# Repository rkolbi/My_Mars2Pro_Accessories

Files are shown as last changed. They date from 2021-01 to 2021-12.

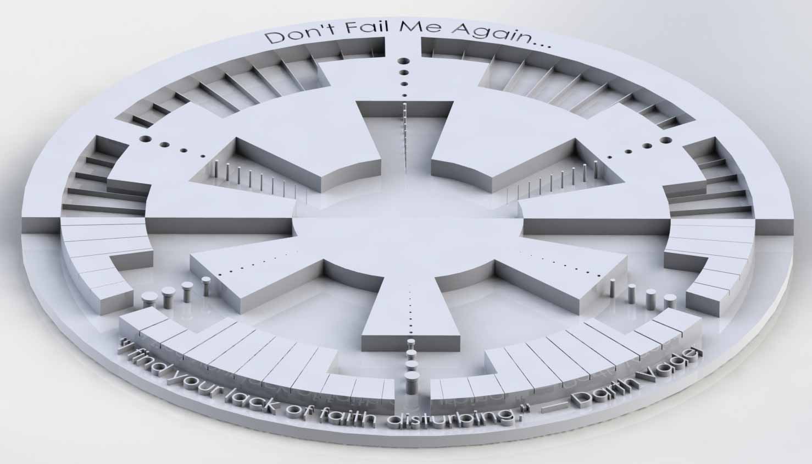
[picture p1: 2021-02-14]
Resin_exposure_testing/STLs/Imperial test/Imperial-resin-v4-c.jpg

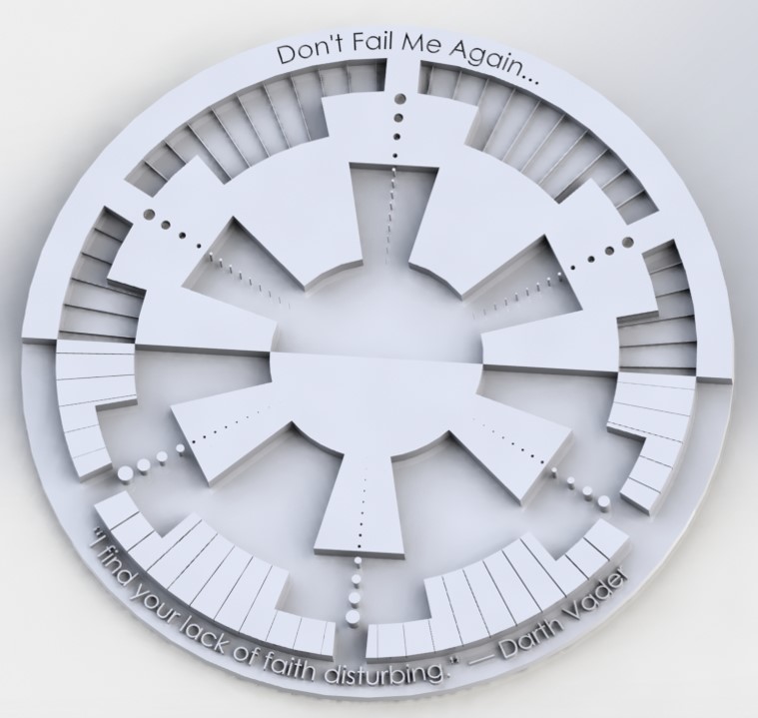
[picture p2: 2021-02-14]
Resin_exposure_testing/STLs/Imperial test/Imperial-resin-v4-a.jpg

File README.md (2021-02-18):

## :milky_way:Various parts, tools, and information for the Elegoo Saturn & Mars2 printers.

Quick links:

**:bulb:Printer guide located [here](MARS-r2.md).**

**:bulb:Downloadable PDF version [here](MARS-r2.pdf).**

**:droplet:MARS2 Pre-sliced resin exposure tests [here](/Resin_exposure_testing/MARS2-Presliced/).**

**:droplet:Resin exposure test STL files [here](/Resin_exposure_testing/STLs/).**

**:droplet:Elegoo Official Resin settings for Elegoo printers [here](/Tools_&_Information/ELEGOO_Resin_Settings_for_Elegoo_Printers(Official).pdf).**

**:droplet:Resin label (Avery 18163) [here](resin-label-avery18163.doc).**

**:wrench:G-Code helper files [here](/Tools_&_Information/gcode/).**

**:wrench:Saturn and Mars2 parts [here](/Parts_STLs/).**

**:wrench:rPi + mariner + Samba walkthrough & config files [here](/Tools_&_Information/my-mariner-configs/).**

<br><br>
:zap: If you have any suggestions for a change, addition, or correction to the guide - please feel free to either submit it [here](https://github.com/rkolbi/My_Mars2Pro_Accessories/issues/new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) or in the discussions page [here](https://github.com/rkolbi/My_Mars2Pro_Accessories/discussions/categories/printer-guide).  
:zap: If you have any questions about anything else here, please feel free to use the discussions page [here](https://github.com/rkolbi/My_Mars2Pro_Accessories/discussions).

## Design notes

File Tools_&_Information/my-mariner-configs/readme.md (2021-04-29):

## Installing mariner + Samba

**Example configuration files can be found [here](https://github.com/rkolbi/My_Mars2Pro_Accessories/tree/main/Tools_&_Information/my-mariner-configs). Mariner GitHub [here](https://github.com/luizribeiro/mariner), author's step-by-step [here](https://l9o.dev/posts/controlling-an-elegoo-mars-pro-remotely/)**.

-Download the latest version of [Raspberry Pi Imager](https://www.raspberrypi.org/downloads/) and install it.

-Connect an SD card reader with the SD card inside.

-Open Raspberry Pi Imager, select CHOOSE OS ->  Raspberry Pi OS (other) -> Raspberry Pi Os Lite.

-Choose your sd-card with CHOOSE SD CARD, then select write.

-Once completed, you should see the contents of the freshly written sd-card.

-Place <u>ssh</u> (this is supposed to be an empty file) & <u>wpa_supplicant.conf</u> files in the sd-card's root directory and then safely eject from OS.

-Insert the sd-card into the rPi and then apply power to the rPi.

-Download and install [Putty](https://www.chiark.greenend.org.uk/~sgtatham/putty/latest.html). Run the Putty Application. Enter `raspberrypi.local` as the address you wish to connect to in Putty. Click OK/Yes if you get a security warning. When prompted on a black terminal window, enter `pi` as your username and `raspberry` as your password.

$`sudo raspi-config`: system options -> Password (enter a new password), system options -> hostname (enter `mariner`), advanced options -> expand filesystem, Finish -> reboot

-Close Putty, wait a few minutes for rPi to reboot, Open Putty, use `mariner` or  `mariner.local` as address to connect to, and use pi as username and new password as just changed.

$`sudo apt-get update && sudo apt-get -y upgrade`

$`sudo nano /boot/config.txt` -> add the following lines to the end of the file:  
```
dtoverlay=dwc2,dr_mode=peripheral  
enable_uart=1
```
Then ctrl+o, ctrl+x

$`sudo nano /boot/cmdline.txt` -> add `modules-load=dwc2` to the end of the line. Remove `console=serial0,115200`
Should look like: 
```
console=tty1 root=PARTUUID=BLAHBLAHBLAH rootfstype=ext4 elevator=deadline fsck.repair=yes rootwait modules-load=dwc2
```
Then ctrl+o, ctrl+x

$`sudo dd bs=1M if=/dev/zero of=/piusb.bin count=4096`
*This can take several minutes

$`sudo mkdosfs /piusb.bin -F 32 -I`

$`sudo mkdir /mnt/usb_share`

$`sudo nano /etc/fstab`

Add the following line to the end of the file:
`/piusb.bin            /mnt/usb_share  vfat    users,umask=000   0       2`
Then ctrl+o, ctrl+x

$`sudo mount -a`

$`sudo nano /etc/rc.local` Add the following before the exit 0, so it looks like this:
```
/bin/sleep 5

modprobe g_mass_storage file=/piusb.bin removable=1 ro=0 stall=0

/sbin/iwconfig wlan0 power off

exit 0
```
Then ctrl+o, ctrl+x

$`sudo reboot`

$`sudo systemctl stop serial-getty@ttyS0`

$`sudo systemctl disable serial-getty@ttyS0`

$`sudo apt-get install samba winbind -y`

$`sudo nano /etc/samba/smb.conf`
Add the following to the end of the file:  
```[mariner]  
[USB_Share]
   comment = Saturn
   path = /mnt/usb_share/
   browseable = Yes
   writeable = Yes
   only guest = no
   create mask = 0777
   directory mask = 0777
   public = yes
   read only = no
   force user = root
   force group = root
```

Then ctrl+o, ctrl+x  

$`wget https://github.com/luizribeiro/mariner/releases/download/v0.1.1-1/mariner3d_0.1.1-1_armhf.deb`

*updated - see here: https://github.com/luizribeiro/mariner/releases*  
$`wget https://github.com/luizribeiro/mariner/releases/download/v0.2.0-1/mariner3d_0.2.0-1_armhf.deb`

$`sudo apt install ./mariner3d_0.1.1-1_armhf.deb`

$`sudo reboot`

-Once rebooted, open windows file explore and type your printer's nick-name as `\\mariner\`
You should now see the USB_Share folder. Right click this and map network drive.

If everything is good, you should be able to access the webpage interface by opening http://mariner:5000/ on your browser.

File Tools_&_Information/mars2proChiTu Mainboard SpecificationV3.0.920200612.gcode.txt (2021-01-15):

; [[The comments after the semicolon, please modify the corresponding parameters according to the comments, the commands after the semicolon will be ignored]]
; The basic format is Mxxx Ixxx, Mxxx Txxx or Mxxx Sxxx, where Ixx (the first letter of the letter I, integer, not the number 1) is followed by an integer, which can be decimal or hexadecimal (beginning with 0x) ), Sxx is followed by a floating point number
;

M8513

; [Stepper motor direction control] The direction of I1 and I-1 are just opposite, so if the motor direction is wrong, either change the wiring or change the direction parameter
M8002 I-1; ;X stepper motor direction, I1 or I-1
M8003 I1; Y stepper motor direction
M8004 I-1; Z stepper motor direction

;[XYZ axis extrusion head/platform movement configuration] only affects the actual movement direction of the manual interface button;;;;;;;;;;;;;;;;;;;;;;;;;;
M8005 Z0; 0: Z axis direction, forming support movement,,
; 1: Resin tank movement in Z axis direction
To
;
; [Speed/Acceleration Setting] The speed is in mm/s and the acceleration is in mm/s^2
M8006 I30; The maximum starting speed, when the movement speed exceeds this speed, the speed will be used as the starting speed.
; This speed is mainly to prevent loss of step, if this value is too small, it will cause the rail angle to bulge when rounding
M8007 I15; The maximum orbit speed value (corresponding to the jerk speed in the open source firmware), if the actual orbit speed of the movement is greater than this value,
; Will force the movement to decelerate. When filling, there will be a lot of reciprocating movement, this value is large, noise is large, and it is easy to lose steps.
; This value is small, the speed is slow, when the printing speed is high, the printing quality will be relatively poor
M8008 I1000; Acceleration, the larger the value, the higher the average speed of actual operation, but the noise is also large, the value is small, the actual speed will be smaller,
;
; [[[Step-related parameters]]] After setting the parameters, please print a cube, and then measure the size with a ruler to confirm that the parameters are correct
;
M8009 S0.0125; [mm value of each step of XY] such as 20 teeth, tooth pitch of 2mm (mxl specification, 2gt tooth data is 2mm), 1.8 degree stepping motor,
; 16 subdivision, then (20*2)/((360/1.8)*16)
;M8009 X0.0125 Y0.0125 ;If you need to set X, Y stepper motor parameters independently, you can use this command
;
M8010 S0.000625; [mm value of each step of Z] On non-delta machines, the calculation formula: lead/((360/1.8)*16).

;
; [Various maximum speeds] In order to ensure the stability of the machine, please set according to the actual measurement results
M8012 I200 ;Maximum speed of XY movement mm/s
M8013 I5; The maximum speed of Z movement mm/s

;
;?Return to zero speed?
M8015 I3; The first zero return speed when Z return to zero, the speed is faster, the Z movement speed of the manual interface is also the same as this speed, and the Z-axis lift is also used at this speed
M8015 S30; The zero return speed when XY return to zero, the speed is faster, the XY movement speed of the manual interface is also the speed at which the XY axis moves
M8016 I3; The second zero return speed when Z zero return, the speed is slower, reducing the second zero return speed can improve the repeated positioning accuracy of the limit position, if the parameter is 0, the second zero return will not be performed

; [Speed ??and distance of Z-axis demolding] During demolding, first rise slowly, then rise quickly, then stay for a while, then fall quickly, then fall slowly
M8070 S3; unit is mm; Z demoulding slow rising distance
M8015 P1.0; unit is mm/s; Z demoulding slow rising speed

M8028 S3.0; unit is mm/s; Z demoulding rapid ascent speed
M8016 P3.0; unit is mm/s; Z demoulding fast descending speed, this parameter is also fast ascending speed and slow descending speed in the old version

M8021 S1.7; unit is mm; Z slow down distance
M8020 S1.0; unit is mm/s; Z slow down speed

; When printing [Z demoulding, the total distance of each lifting height, in mm, the distance = slow rising distance + fast rising distance]
M8070 Z7; if movement z is not needed, set it to 0

; [Dwelling time after ascending when Z axis is demolding]
M8016 D0; The unit is ms (milliseconds),
;
; [X, Y, Z maximum stroke] unit is mm
M8024 I0; X maximum stroke, the axis is used for demoulding in the X direction or used for scraping. If the direction does not need to move, the stroke is set to zero, and the manual interface cannot operate scraping. If it is set to non-zero, turn it on The axis will return to zero
M8025 I0; Y maximum stroke, this axis is used to block the lens of the projector, the lens is blocked at the reset position, and the lens is not blocked at the maximum stroke position. If the axis movement is not required, set this parameter to 0, manual interface It can’t be operated either. If a non-zero setting is set, the axis will return to zero after power on
M8026 I165; Z maximum stroke, this stroke is the movement stroke of Z, be sure to measure it with a ruler, set it carefully, after the pause and print, the Z axis will stay at the maximum stroke position
;

;
; [XY axis limit switch position type]

M8029 I0 ;0: Unilateral limit, only X-, Y-, Z- limit is used, Z+ is not used
; 2: Bilateral limit, if Z+ and Z- limit are used at the same time, Z+ can limit the maximum stroke of Z

;
;
;
; [XYZ limit switch wiring type] If this configuration is wrong, when the motor is operated in the manual interface, the motor cannot move in a certain direction and the buzzer
; There will be a dizzying sound.
; Simple judgment method, if the configuration is normal, the buzzer will emit a beep when the position is changed from not limit to limit.
; When the position is changed from the limit position to the limit position, the buzzer will not sound. If the phenomenon is found to be opposite, please modify this configuration
M8029 T0 ;0: limit switch is normally open (when not limit,-and s voltage is high level, when limit is low level)
; 1: The limit switch is normally closed (when the limit switch is not limited, the voltage of-and s is low, and when the limit is high)
;
;?Z-axis limit switch position?
M8029 S0 ;0: Limit when the extruder is closest to the platform, and the limit is connected to Z-
; 1: Limit when the extruder is farthest away from the platform, and the limit is connected to Z+
;
; [Whether the XYZ axis returns to (0,0,0) after homing,]
M8029 C0 ;0: return to XYZ(0,0,0) position, that is, the position where the extruder returns to the coordinate zero position
; ;1: Stay at the limit position
;
;;
;?Fan 1 control?
M8030 I-1 ;>0: If you need to force fan 1 to automatically turn on the fan when the temperature is greater than a certain temperature, set a temperature greater than 0.
;0: If set to 0, the default is not to transfer
;-1: Always open MF
;-2: Open when the file is printed, close EF when not printed
;?Fan 2 control?
M8030 T-1 ;0: If set to 0, the default is not
;1: >0 Once exposed, fan 2 will turn, if no exposure, the fan will stop LED
;-1:<0 Always open MF
;-2: Open when the file is printed, close EF when not printed

;?LED interface control?
M8030 S4; 0: Normally off
; 1: Normally open
;2: Open when the file is printed, close EF when not printed
;3: Close when the file is printed, open when not printed
;4: Once exposed, the LED will turn on, if not exposed, the LED will stop LED

; [Does SD card/U disk support folder display]
M8034 I1 ;0: not supported
; 1: Support
;

;?The warm-up time for the projector to turn on?
M8070 T10; unit is s

; [Projector communication baud rate, if serial port control is not needed, set the baud rate to 0]
M8070 I9600; Projector communication baud rate

;?Projector boot command?
M8070'* 0 IR 001\r'; \r \n \t \x6e can be used to represent special characters such as carriage return, line feed, tabulation, and hexadecimal 0x6e, up to 40 characters

;?Projector shutdown command?
M8071'* 0 IR 002\r'; projector shutdown command
;

;?Machine Type?
M8080 I0 ;0: XYZ common type,

;
; [Thermal resistance type] Temperature sensor type
M8081 I0 ;0: ideal NTC 100K 1% 3950 B,
;
;

;[Z zero point and limit position setting] 0: limit position is the same as Z zero point 1: limit position is different from Z zero point
M8083 I1; The limit position is different from the zero point of Z, it needs to be used with M8084 Z* instruction
;
;
;; [Difference between Z limit point and zero point limit, the value is usually positive]
M8084 Z0; If you want to set the offset in the configuration, please remove the semicolon in front of the command line, and you can also configure the offset automatically through "Set Z to zero" on the interface
;
;
; [Start LOGO time]
M8085 I3000; boot logo duration, minimum 100ms, maximum 6000ms

;?Screensaver time?
M8085 T0; How long will it take to enter the screen saver interface in standby mode, in seconds (s), when it is 0, it means that the screen saver is disabled

; [External drive settings]
M8087 I0 T0; I: The setup time from the direction signal valid to the pulse signal high level, the unit is ns
; T: The shortest hold time of the pulse signal, the unit is ns, if there is no external drive control board, please set it to zero.
; Several external drive parameters: THB7128:I100000 T0 ;;;;TB6560:I40000 T0 ;;;TB6600:I100000 T0
;
;
;
;?Action after printing?
M8489 P3; action after printing
; 0: Turn off all motors,
; 1: No action after printing,
; 2: After printing is completed, return to zero, and the motor will not be powered on
; 3: After printing is completed, it will drop to the maximum stroke of Z, and the motor will not be powered

;
;???????Save Parameter???????This parameter must not be less, otherwise the parameter cannot be saved to the device
M8500; save configuration
;
More about this source text
Source text required for additional translation information
Send feedback
Side panels

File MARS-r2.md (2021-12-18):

# :milky_way:Elegoo Mars Printer Guide

## TABLE OF CONTENTS

·  [SAFETY](#point_upSAFETY)

·  [GETTING STARTED](#keyGETTING-STARTED)

·  [OPERATING ENVIRONMENT](#partly_sunnyOPERATING-ENVIRONMENT)

·  [POWERING ON THE PRINTER](#electric_plugPOWERING-ON-THE-PRINTER)

·  [BUILD-PLATE LEVELING](#roller_coasterBUILD-PLATE-AND-LEVELING)

·  [MODEL SETUP & SETTINGS](#microscopeMODEL-SETUP-AND-SETTINGS)

·  [STARTING A PRINT](#rocketPRINTING)

·  [CLEANING THE PRINT](#star2CLEANING)

·  [POST PROCESSING THE PRINT](#hammerPOST-PROCESSING)

·  [FEP MAINTENANCE](#oceanFEP-MAINTENANCE)

·  [PRINTER MAINTENANCE](#nut_and_boltPRINTER-MAINTENANCE)

·  [CONSUMABLE ITEMS](#heavy_check_markCONSUMABLE-ITEMS)

·  [ACKNOWLEDGMENTS](#thumbsupACKNOWLEDGMENTS)

## :question:How does this printer work?

**Your Elegoo is a <u>M</u>asked <u>S</u>tereo<u>L</u>ithography <u>A</u>pparatus resin printer or MSLA for short.** The word stereolithography comes from the Greek word stereo, meaning solid, and (photo)lithography, a form of 'writing' with light. Stereolithography with your 3D printer does precisely that, drawing solids with light one layer at a time. Masked Stereolithography Apparatus(MSLA) utilizes a 405nm wavelength LED array as its light source and an LCD photomask to shape the LED array's light image. The LCD photomask is digitally displayed and composed of square pixels. Then individual pixels are deactivated on the LCD to allow the LED light to pass through to form the resulting layer.

The printing process starts as the build-plate descends into a resin vat, leaving space equal to the layer height between the build platform, or the last completed layer, and the bottom of the vat. The LCD mask then selectively allows UV light to pass through it, shining the light upward through the vat's bottom and curing a layer of resin. 

The cured layer then gets peeled from the bottom of the vat as the build platform moves up, pulling the layer off the FEP(fluorinated ethylene propylene) film. In essence, this is a tug of war between the build-plate surface and the FEP film. The build-plate usually wins this challenge as it remains flat, not allowing any edges to start peeling. The FEP film however is non-stick, highly flexible, and purposely loose. When the cured layer gets pulled upwards by the build-plate, the FEP film curves, letting the cured layer's edges begin to break free as the build-plate rises - breaking the surface suction force and yielding a peel. Once the layer is detached and raised, the fresh resin flows beneath, and the process repeats until the print is complete.

:bulb:To allow the tug of war to work in favor of yielding a successful print, the FEP has to remain non-stick and flexible, the resin has to stay viscous, and the build-plate needs to bond to the resin. Assuming the item to be printed has been orientated and sliced correctly, the easiest way to ensure success is to keep the build-plate and FEP clean, operate the printer at a room temperature of 21'C and above, and have a leveled build-plate. Regarding temperature, always check the resin manufacturer's data as some require it to be a bit higher.

## :point_up:SAFETY

#### Before you start printing, remember safety first and read the owner's manual!

Always handle resins as though they are toxic unless you have specific documentation that states otherwise. Unless otherwise stated, resins are not approved for use with food, drink, or medical application on the human body. Never ingest resin in liquid or solid form. If swallowed, immediately call a poison center or medical professional.

· Ensure you're working in a well-ventilated area. Do not eat, drink, or smoke in the printing work area. Remove jewelry (rings, watches, bracelets) before handling uncured UV curable materials. 

· Always wear proper eye protection and a mask when exposed to any uncured resin, whether during print preparation, printing, or post-processing. Ensure you are wearing chemical-resistant gloves, butyl, nitrile, or neoprene. Avoid using latex gloves.

· Ensure your body is adequately protected by clothing in case of spills and splashes. In case of spillage, if resin makes contact with skin or eyes, wash thoroughly with hand soap and water and seek medical advice - do NOT use solvents to wash - do NOT wash with hot or warm water - this will open your pores and may allow the resin to be pushed further into your skin.

· Tools that may be contaminated with the material should be cleaned before reuse with window cleaner or plenty of denatured or isopropyl alcohol, followed by thorough washing with soap and water.

· Do note that photopolymer resins exothermically react with light, especially UV, and can produce very high heat.

## :partly_sunny:OPERATING ENVIRONMENT 

·  Always place the printer on a stable surface, where it cannot fall or tip over. Avoid placing the printer over carpeted areas or use a barrier to avoid the possibility of carpet damage.

·  Keep your workspace environment, containing your printer, resin, and cleaning/UV curing station, at a stable room temperature not less the 72f - ideal being 75f to 85f. Cold resin presents two main issues, increased viscosity and slowed/unstable/unpredictable curing rates. Viscosity refers to the resistance to flow; the lower the viscosity, the easier it flows - we want low viscosity. When the resin is cold and thick, it is hesitant to mix well and, more importantly, increases build-plate and part suction to the FEP, leading to potential failures. During these colder operations, your printer's FEP may have less flexibility and elasticity, further increasing the potential of failure. For the curing rate, the higher the temperature, the faster the resin will cure. On the flip side, increased exposure times compensate when the temperatures are below the recommended temperature envelope, but the required exposure can be unpredictable and change as the print progresses. Most resin manufacturers provide recommended/ideal operating temperatures; some even offer recommendations for colder environments. Additionally, higher room temps may be necessary to achieve complete polymerization, depending on the resin used.  
Always visit the manufacturers' website for the most current guidance as each type and color of resin can, and most likely will, have different requirements. With that, make sure you are using the recommended settings for your printer.  

·  Remember that when 'reading' your room temperature, the temperature you read may differ from what your printer is exposed to. An easy example of this would be 'reading' the temperature from an interior wall-mounted thermostat while your printer is on an exterior wall - next to an opened or cracked window. Additionally, many people have thermostats that lower the temperature at night - ensure the room temperature stays stable during the print process.  

·  Although not optimal, you can take the following steps to increase your success rate when operating in colder environments. Remove the build-plate, ensure it is clean and free of any resin or debris. Take the resin bottle, ensuring the cap is on snugly, and wrap it and the build-plate in a heating pad and warm until it is at the proper temperature. Once the resin and build-plate are fully warmed, clean the build-plate surface with alcohol and a lint-free cloth, pour your resin into your vat, and start your print as usual. Lastly, the printer and resin will generate a small amount of heat during the print. By placing the shipping box over the printer during the print, you may be able to capitalize on this and retain some needed warmth.  

## :key:GETTING STARTED

·  [PLACE THE PRINTER ON A STABLE, FLAT SURFACE](#partly_sunnyOPERATING-ENVIRONMENT)

·  [APPLY POWER TO THE PRINTER](#electric_plugPOWERING-ON-THE-PRINTER)

·  [LEVEL THE BUILD-PLATE](#roller_coasterBUILD-PLATE-AND-LEVELING)

·  [PREPARE AND PRINT THE TEST FILE](#rocketPRINTING)

·  [CLEAN THE PRINTED TEST FILE](#star2CLEANING)

·  [CURE THE PRINTED TEST FILE](#hammerPOST-PROCESSING)

## :electric_plug:POWERING ON THE PRINTER

·  Place the power cord so you cannot trip over it, step on it, or inadvertently unplug it.

·  Check the power adapter, ensure it's firmly plugged into the wall outlet - you should see a blue LED (on the transformer brick) to indicate that it has mains power.

·  Plug the DC end of the power adapter into the receptacle at the rear of the printer. Check the power switch is in the "ON" position.

·  The front LCD touch panel should greet you with a graphical display.

## :roller_coaster:BUILD-PLATE AND LEVELING 

As touched on in the front matter, the printing process starts with the build-plate descending into the resin vat, leaving space equal to the layer height between the build-plate and the vat's bottom FEP lining. An improperly leveled build-plate will cause this space to be too large leading to failed print with harden resin stuck to the vat's bottom, or too small making the Z-axis bottom-out - causing the stepper motor miss steps and emit a vibrating / grinding noise. 
Make sure you take the time to level your build-plate correctly. Do not rush this step in your hurry to start printing, take time and get it right. Once your build-plate is leveled correctly and locked down tight, you do not have to relevel it anymore unless you make other adjustments that affect the build-plate. *Do not confuse build-plate leveling with adjusting the four legs of the machine - which is leveling the machine itself.*

**How do I level my build-plate?** 

It is highly recommended that you use the official method, aka paper method, if you're using standard FEP film thickness (100~200um). Watch the Official Elegoo Leveling instructional video [here](https://youtu.be/tiHu3o72NDw), and the reset Z=0 instructional video [here](https://youtu.be/cqRBZUAEWD4). 3dPrintingPro covers leveling and associated issues [here](https://youtu.be/Zh9dx1fKnqI).

**:wrench:Preferred Method - Step by step follows:**  
- [ ] If the build-plate is not at least halfway up, raise it by selecting the 'Tool' Button, 'Manual' Button, '10mm' Button, then Up Bottom. Each time you press this, it will raise only 10mm, so you may have to press this multiple times.  
- [ ] Remove the build-plate by turning the top black rotary knob (on the Z-axis) in a counter-clockwise direction, enabling the build-plate to be slid towards you. Do not remove the rotary knob; only rotate it enough to slide the plate off.  
- [ ] Optional but recommended: Test the UV light source by selecting the 'Tool' button, 'Exposure' button, adjust for a few seconds and select the 'Next' button to begin.  You should see a complete rectangular image on the top LCD; the front touchscreen should display the same.  
- [ ] Ensure the build-plate surface is clean and free of any resin or gunk; gently scrape if needed. Clean the build-plate surface with alcohol and lint-free cloth.  
- [ ] Loosen the two bright hex-head bolts on the build-plate head using the large hex wrench - one is on the front, the other on the side. Do not unscrew completely, just enough to allow the build-plate to rotate freely as well as up and down.  
- [ ] Remove the resin vat and place it on its side, in an area where you won't knock it. Check the top LCD free and clean. If dust or residue is present, remove using a clean microfiber cloth - apply alcohol if needed. !Only use microfiber cloth!  
- [ ] Get a standard sheet of printer paper, cut it in half, and place it over the top LCD screen.  
- [ ] Slide the build-plate back onto the printer's Z-axis and tighten the rotary knob.  
- [ ] Home the Z-axis by selecting the 'Tool' button, 'Manual' button, and Home button (looks like an upside-down T).  
- [ ] The build-plate will go down to the paper, slightly rise, and then down again. Check the build-plate's alignment and rotate as needed to ensure it is square with the printer.  
- [ ] While gently pressing down on the build-plate, ensuring it is completely flat and square, tighten the forward-facing hex-head bolt first, followed by the side facing.  
- [ ] Gently try to pull the paper out, not all the way but just only by a few millimeters or so. Try the pull test from the left and then the right edges. If the paper is unable to move, raise the build-plate 0.1mm by first selecting the '0.1mm' button, followed by the Up button - this is not always required, only if you feel the paper will tear when pulling. :warning:If one side was easier to pull the paper than the other, you will have to readjust by loosening the securing screws and go up three steps. If this is a continuing problem, see the notes following the leveling section.:warning: 
- [ ] Select the 'Z=0' button, and select confirm.  
- [ ] After setting Z=0, verify that it is set correctly by starting a dry-run print, leaving the piece of paper on the screen, and checking that the build-plate starts the first layer at the correct Z=0 position have set. !Remember that Z=0 is not the same as Home.  
- [ ] Raise the build-plate by pressing the 10mm button, followed by the up button, at least seven times. Remove the paper.  
- [ ] Grab the resin vat. Check it free and clean - both sides. And again, check the top LCD free and clean. If dust or residue is present, remove using a clean microfiber cloth - apply alcohol if needed. !Only use microfiber cloth!  
- [ ] Gently slide the resin vat into position, taking care to glide it in with a slight upward force against the securing towers and not the LCD screen (the vat film and LCD screen scratch quickly). Ensure the vat is in place before screwing in the two-tower side bolts by feeling a small detent position where it sits securely without wobble. The max resin fill indication should be visible from the front, and the resin pour-out groove should be furthest from you on the left.

**:wrench:Alternate Method 1 / Clean & Empty VAT in place - Step by step follows:**  

- [ ] If the build-plate is not at least halfway up, raise it by selecting the 'Tool' Button, 'Manual' Button, '10mm' Button, then Up Bottom. Each time you press this, it will raise only 10mm, so you may have to press this multiple times.  
- [ ] Remove the build-plate by turning the top black rotary knob (on the Z-axis) in a counter-clockwise direction, enabling the build-plate to be slid towards you. Do not remove the rotary knob; only rotate it enough to slide the plate off.  
- [ ] Ensure the build-plate surface is clean and free of any resin or gunk; gently scrape if needed. Clean the build-plate surface with alcohol and lint-free cloth.  
- [ ] Loosen the two bright hex-head bolts on the build-plate head using the large hex wrench - one is on the front, the other on the side. Do not unscrew completely, just enough to allow the build-plate to rotate freely as well as up and down.  
- [ ] Check the FEP free and clean. If dust or residue is present, remove using a clean microfiber cloth - apply alcohol if needed. !Only use microfiber cloth!  
- [ ] Slide the build-plate back onto the printer's Z-axis and tighten the rotary knob.  
- [ ] Home the Z-axis by selecting the 'Tool' button, 'Manual' button, and Home button (looks like an upside-down T).  
- [ ] The build-plate will go down to the FEP, slightly rise, and then down again. Check the build-plate's alignment and very gently rotate as needed to ensure it is square with the printer.  
- [ ] While gently pressing down on the build-plate, ensuring it is completely flat and square, tighten the forward-facing hex-head bolt first, followed by the side facing.  
- [ ] Select the 'Z=0' button, and select confirm.  

**:wrench:Alternate Method 2 / Resin Filled VAT in place - Step by step follows:**  

- [ ] If the build-plate is not at least halfway up, raise it by selecting the 'Tool' Button, 'Manual' Button, '10mm' Button, then Up Bottom. Each time you press this, it will raise only 10mm, so you may have to press this multiple times.  
- [ ] Remove the build-plate by turning the top black rotary knob (on the Z-axis) in a counter-clockwise direction, enabling the build-plate to be slid towards you. Do not remove the rotary knob; only rotate it enough to slide the plate off.  
- [ ] Ensure the build-plate surface is clean and free of any resin or gunk; gently scrape if needed. Clean the build-plate surface with alcohol and lint-free cloth.  
- [ ] Loosen the two bright hex-head bolts on the build-plate head using the large hex wrench - one is on the front, the other on the side. Do not unscrew completely, just enough to allow the build-plate to rotate freely as well as up and down.  
- [ ] Ensure there are no solidified/hardened pieces of resin present in the VAT. Ensure the FEP surface is smooth by gently raking a soft silicone spatula across all of its surface areas. :warning: If roughness exists, stop the leveling process, filter the VAT's contents back into the resin bottle, clean the VAT, and then restart leveling :warning: Damage to the FEP and LCD screen is possible when debris exists between the FEP and build-plate.   
- [ ] Slide the build-plate back onto the printer's Z-axis and tighten the rotary knob.  
- [ ] Home the Z-axis by selecting the 'Tool' button, 'Manual' button, and Home button (looks like an upside-down T).  
- [ ] The build-plate will go down to the FEP, slightly rise, and then down again. Check the build-plate's alignment and very gently rotate as needed to ensure it is square with the printer.  
- [ ] While gently pressing down on the build-plate, ensuring it is completely flat and square, tighten the forward-facing hex-head bolt first, followed by the side facing.  
- [ ] Select the 'Z=0' button, and select confirm.

**How tight to the paper should I level the build-plate?**

When using the recommended paper method, the paper should be tight enough to pull out with even resistance but not push back in. Remember that the build-plate must grip the paper evenly. 

**Remember** that as you tighten the front and side securing screws, it can move the plate by a tiny fraction - when tightening the bolts, always keep a hand gently pressing the build-plate down and level. When done, if you will find that you cannot pull the paper without tearing, you should raise / backoff the build-plate level by 0.1mm (100um) until the plate is gripping the paper with even resistance and that you can pull but not push it back. This usually requires just one raising of 0.1mm. Lastly, whether you had to raise the plate or not, set Z=0.

**What type of paper should I use to level the build-plate?** 

Just regular photocopy paper, they're generally around 80gsm, but any paper 70 ~ 120gsm (average thickness ranging from 0.05 to 0.10mm) should work too. Just ensure that the paper is clean and not creased or folded. 

**I tried to level the build-plate, but one side is tighter than the other?** 

Using your fingers, push the opposite side of the plate when tightening the set bolts. Alternatively, if you're using the paper method, you can slip another strip of paper to the side, which is too tight, and then tighten the screw. You may need to try this a few times to get the perfect level. 

**I set Z=0, but when I press Home, the position is different?**

**Home is not Z=0!** Home is fixed; it is the hardware Z endstop. Unless you change it physically, it will always be in the same position. Z=0 is the offset distance between Home and your LCD screen; you define during the leveling process when you set Z=0, that's why you have to Home first, then move the platform, then set Z=0. 

When a new Z=0 is specified, pressing Home will NOT move the platform to the position you set; it will be the start position when a print is initiated. You can check it by removing the vat and starting a print.

As said, improper leveling contributes to a lot of frustration, mostly because of its mechanics' poor documentation. Here is an example to consider; let's say you are leveling the printer, loosened the screws, and press home. You tug on the paper, it feels tight, so you raise by .1mm, then hit 'Z=0' because you raised Z. With this, once you home again, the build-plate will still stop at mechanical zero because of homing stops at the endstop trigger. If you looked at the electrical position of Z, it would read Z:-0.1. Now we know that when we initiate a print, it will home and then go to Z offset (raise .1mm), and then start printing.

Flash forward several prints later, and you level the machine again. You place your piece of paper on the LCD, loosen the screws, and press home. This time you tighten the screws and then remove the paper with no significant tension/friction and think that you don't have to press 'Z=0' because you didn't move Z to take out the paper... WRONG - This is what gives people issues - IF you don't press Z=0, the printer will still have an offset of 0.1mm from the previous leveling, and you may run into problems due to incorrect leveling - because it's 0.1mm off. Remember, homing goes to mechanical zero when the endstop is triggered and doesn't care about the offset!

*Try this for fun: Home and then raise Z by 10mm, press Z=0, and then home again to see where it stops - it will stop when the endstop is triggered, and it will seem as if the Z=0 did nothing. Then, with vat out and no resin, start a print - it will home and then begin to print 10mm above the LCD. So, long story short, when leveling and you're happy with the paper pull test - whether you bumped Z height or not, press 'Z=0'.*

**Do I have to relevel my build-plate after every print?**

No, this should not be required. If you have correctly leveled, securely tightened, and locked down the build-plate tight, it will remain in place and correctly leveled for a very long time. You only need to relevel your build-plate if it has slipped, been knocked, or you made changes that affect the Z=0 position. 

**Should I sand my build-plate?**

Sanding is the last resort you should attempt, and only when you have verified that the build-plate surface is not flat.

## :microscope:MODEL SETUP AND SETTINGS

**How do I use Chitubox slicer?**

CHITUBOX has an excellent article repository [here](https://www.chitubox.com/en/support/indepth/technology), this should be your first stop. In addition, lots of video tutorials exist on YouTube - 3DPrintingPro has an excellent set [here](https://www.youtube.com/watch?v=TTZpvhfaNWY&list=PLC4QzbTxrEF-fA1OC_-zE_4f6n1K-w2SS).

**What settings do I need for the test (rook) file?** 

The test file that came on the included USB stick has been pre-sliced and settings configured for generic resin. Please see the [Printing](#PRINTING) portion of the guide for directions on how to obtain the best results with this file. 

**How should I orientate my part?**

By orientating the part in different directions, there can be a significant difference in the print quality. Sudden changes in the layer's cross-section, small to large or vice versa, will lead to a drastic volumetric change of exposed resin, affecting each layer's shrinkage. In severe instances, this can affect inter-layer adhesion but almost always will result in visible surface lines. CHITBOX has a good article on this topic [here](https://www.chitubox.com/en/article/support/howto/chitubox-free/editing/25). 3DPrintingPro's related video is [here](https://www.youtube.com/watch?v=8xolVj0izVo&t=19s). 

Lastly, vary the placement of your part on the build-plate. If you consistently place your objects in the build-plate's center, your FEP will prematurely wear out in the center yet be absolutely fine in the surrounding, unused, wasted areas.

**What angle should I use to minimize layer lines?**

There isn't one best angle for printing everything. It really depends on your layer height and the type of model you're printing. Don't forget that model orientation also plays a big part in determining the best angles. You could actually be losing details printing at the wrong angle for the layer height. See a detailed explanation [here](https://www.youtube.com/watch?v=Qs2Rb0ExnIM). 

**I bought x resin; what are the best settings for it?** 

Every resin behaves differently; there are no best settings that will work for every resin and every machine. For a quick start, you can refer to the [community resin exposure settings](https://www.elegoo.com/pages/3d-printing-user-support). Those settings should enable you to get a print going quickly, but you will need to test and adjust from there to find the best settings applicable for your machine. 

Casting resins can have a difficult time bonding to the build-plate, and subsequently ruining your print. There are multiple ways to increase adhesion during printing. The easiest option would be to change the profile settings, increase the number of bottom layers, and simultaneously increase the bottom curing time, increasing adhesion. If that doesn't work, apply resin on the build-plate surface and leave for 3 mins before printing. If issues persist, apply a thin layer of primer (can be the very resin you are using) on the plate to improve adhesion - Apply to the build-plate and keep under UV light for 10 to 15 minutes. Your last resort would be to rough up the build-plate by scrubbing it with a clean 'cooking pan' abrasive pad, using a circular motion, covering the entire plate while it is flat on the working surface, and then going through the above steps again. A good video applying primer [here](https://www.youtube.com/watch?v=eDl3vzZy0qQ).

**How do I find the optimal settings for my resin and machine?** 

It's usually best to start with the community resin exposure settings and then dial them in with a few test prints. These test prints will allow you to obtain the optimum settings for your resin, in your environment, matched to your machine. A good instructional video can be found [here](https://www.youtube.com/watch?v=r9GwPEJ8Lq8).

**Resin storage**

Store resins at room temperature in a tightly-closed container away from direct sunlight, preferably in a leak-proof bag. When choosing a storage location, remember that although your room temperature may be adequate, locations at floor level and against exterior walls can expose the resin to varying temperature fluctuations. Inspect the bottles for leakage every couple of weeks, ensure that the caps are on tightly, and give a quick shake to ensure the resin components stay uniformly mixed.

**My resin is expired, can I still use it?** 

Generally, most resin manufacturers advise using the product within one year. These are basically "use by" dates, not expiry per se. In practice, if it was stored at room temperature, in a tightly-closed container, and had no contamination from any cleaning products - It should be acceptable for use. Start by giving the resin a good shake mixing. When pouring it from the bottle to the vat, use a paint filter to catch any particulates that may be present, pay attention to how it flows out of the bottle; it should have a smooth uniform flow as you'd expect with no lumps, chunks, or crystals. Lastly, do a small/quick test print so you can avoid wasting time down the road.

**What do the print settings mean?**

This is assuming you're using the Chitubox slicer that is included on the USB stick. Other slicers may use different terminology, but they're functionally the same. If you're just starting, it's highly recommended you use the Chitubox slicer. It's basic, won't overwhelm you with bells and whistles, and just works. 

**·  Layer Height:** As the name implies, layer height is the exact height of each cured layer. Layer thickness affects not only the speed (printing time) and the quality of each print. The number of layers required to create an object determines the printing speed and the printing time required. The thinner the layer thickness, the longer it takes to make a 3D printed object of a given height. While relatively, with a slimmer layer height, you will increase the quality of the print, leading to a smoother surface and more detail visible in the Z-direction (height) of the model.
Generally, the printers' minimum functional layer height is 25 µm (0.025mm) layer height, and the maximum is 100 µm (0.1mm) layer height. You can adjust this setting based on your printer's actual situation, given the object and resin. If you have no idea how to choose the right one, the tried-and-true technique is to start with a layer height of 50 μm (0.05mm).

**·  Bottom Layer Count:** Simple, this one it's about how many of those super hard base layers to lay down on the base of your print usually this is 5-8 layers.

**·  Exposure Time:** The print quality for each 3D resin is also affected by the light power and the curing or exposure time. Exposure Time is the amount of time that the light source will expose each layer during printing. Different Mars printers have different cure times for various resins, with the mono LCD equipped units requiring about two-thirds less time. 

**·  Bottom Exposure Time:**  Same as *Exposure Time* but only applies to the bottom layers, as set in the *Bottom Layer Count*.

**·  Light-off Delay:** This is the amount of time that the UV light is turned off between the end of one exposure cycle and the beginning of the next. After exposure, the UV light turns off, the build-plate lifts and peels, and then descends; ready for the next cycle and will wait at the bottom (resting at the set layer height over the FEP sheet, at the bottom of your vat) before the UV light comes on again for the next exposure cycle. Longer off-times leave more time for the resin to settle out and form a new layer with fresh resin. This is especially useful for more viscous resins to mitigate issues of poor definition of surfaces facing the build-plate.

**·  Bottom Light-off Delay:** Same as *Light-off Delay* but only applies to the bottom layers, as set in the *Bottom Layer Count*.

**·  Lifting Distance:** This is how far the Z-Axis will pull up upon completion of the exposure cycle.

**·  Bottom Lift Distance:** Same as *Lifting Distance* but only applies to the bottom layers, as set in the *Bottom Layer Count*.

**·  Lifting Speed:** Lift speed refers to the rate at which the build-plate is lifted from the resin vat between layers. When lift speed is too fast, the model and supports can be broken or damaged due to the tug of war between the build-plate and the FEP film. But if reduced too much, the printing time will be unnecessarily increased. When modifying this setting, you should take both print quality and print time into account. 

**·  Bottom Lift Speed:** Same as *Lifting Speed* but only applies to the bottom layers, as set in the *Bottom Layer Count*.

**·  Retract Speed:** This is how quick the Z-axis will plunge back into the vat, after it has completed it's lift cycle. This setting applies to both normal and bottom settings.

**·  Anti-aliasing:** Aliasing is the staircase effect that occurs when diagonal or curved lines or borders are drawn on raster displays consisting of square or rectangular pixels. Anti-aliasing is to smooth object edges by reducing the number of lines and vertical artifacts you see on your 3D printed model.
CHITUBOX provides an anti-aliasing function with a 2/4/8 level. After special algorithm processing, it makes the model more smooth and effectively reduces edge aliasing.

**·  Transition Layer Count:** This is the number of layers where the bottom and normal exposure times will gradually decrease rather than an abrupt drop, aiding the adhesion between them.   At present, this is only available for the ELEGOO SATURN, and the transition type is linear only.

**What is cupping / suction warping, and how do I combat it? Should I add a vent hole?**

Vent holes are often improperly called "drain" holes; they are not for draining resin. Imagine a glass full of water upside down in a bucket of water. When you pull the glass up out of the bucket, it stays full until the lip of the glass breaks the surface of the water in the bucket. 

In the vat, the lowest point of the print, the new layer does not generally rise above the vat's liquid resin level. Therefore, the liquid resin inside the "bowl" or "cup" cannot evacuate unless you add a vent hole. This is a significant cause of failures. You have to reduce the work that the stepper motor has to do to lift the platform.

Initially, in the printer's vat, the inside volume of resin will be pulled up. Eventually, depending on the volume of the inside space and the volume of resin in the vat, the new layer will rise above the fluid level because the surface of the fluid will be moving down at ever-increasing rates with each layer. That is, the level of the fluid inside the space and in the vat are actually moving in opposite directions. When that happens, all of the fluid inside will be released, but now you have a trapped volume of air, so you will alternate between struggling with lifting up and struggling with pushing down. 

Without vent holes, it's a recipe for bad prints. The result is that you can get multiple failures at various heights, depending on where these extremes occur. 

**How do I hollow my model?**

It depends on the software. Two popular free programs that make it easy to hollow your models are Chitubox and Meshmixer. Look [here.](https://www.youtube.com/watch?v=wAW-rqrr8nc)

**Can I just use auto supports for all my models?** 

Not the best idea. For simple models, auto supports should generally work, but as with anything automatic, it will never be perfect. For a start, you can use auto supports and supplement with manual supports on parts that the software missed. But it will be best to [learn to place your supports manually](https://www.youtube.com/channel/UCbv2mDrRqXovPdahRyoCFhA/search?query=supports) and precisely; you will find that you will need less supports and produce better prints in the long run. 

## :rocket:PRINTING

:exclamation:*Ensure you are operating your printer with an ambient room temperature of at least 21'C / 70'F, 25'C / 77'F being ideal. This is critical for success as it greatly affects the resin and FEP film properties.*

**My first print, do I have to print the rook?** 

:wrench:It is recommended that you print it, but before you print the rook file from the USB stick, there are some steps you need to take to ensure success.

- [ ] Check your resin's bottom & normal exposure times, for your printer model, [here](https://github.com/rkolbi/My_Mars2Pro_Accessories/blob/main/Tools_%26_Information/ELEGOO_Resin_Settings_for_Elegoo_Printers(Official).pdf).
- [ ] Plug the USB stick in your computer and open the __Rook.ctb file in Chitubox slicer, you should just have to double-click on the file to open it. 
- [ ] Once it opens the file, you will see two columns of numerical data in the lower portion of the screen. Check that 'Exposure Time(s):' and 'Bottom Exposure Time(s):' match the numbers corresponding to your printer/resin in the excel spreadsheet above. 
- [ ] If the numbers in Chitubox differ from the spreadsheet, double-click the number to change and type the value obtained from the spreadsheet.
- [ ] Click the 'Save' button and call the file '__My-Rook.ctb'. Safely eject the USB stick from your computer.
- [ ] Inspect the build-plate surface and ensure it is free of any debris. Give it a good wipe down with IPA and a lint-free cloth. Ensure the build-plate a firmly secured by snugging the black rotary knob.
- [ ] Inspect the FEP film on the bottom of the resin vat. Make sure it is clean and clear, free of any holes, deep dents, and deep scratches. Ensure the resin vat is secured by snugging the two vat screws.
- [ ] Identify the max file line in the resin vat. Pour your prepared resin into the vat, filling it halfway - to a level between the FEP film and the max fill line. If any air bubbles exist, wait a few minutes for them to dissipate.
- [ ] Plug the USB stick in to your printer, select the '__My-Rook.ctb', and commence the print.

A successful test print with a known-good model will confirm that your printer works as it should and that you have precisely leveled your build-plate and your FEP tension is correct. It is also inevitable that sooner or later, a print will fail. A failed print will often leave small, partially cured resin pieces floating in the vat or hard cured resin stuck to the FEP. For subsequent prints to have the highest success rate, the resin vat must be cleaned and cleared of debris.  Although it is not required, it is good practice to inspect and clean the vat after every print.

**I'm about to start a print, but the touchscreen shows a filename highlighted in red?** 

That's normal; it's showing the last file you selected or printed. 

**I can't see my files on the touch screen**  

·  Ensure the memory stick is USB 2.0, from a reputable manufacturer, formatted as MS-DOS (FAT32), and between the sizes of 1GB to 16GB.  
·  Ensure the memory stick is directly connected to the printer and not being run through numerous extension cables.  
·  Ensure that you properly eject the memory stick from your computer after writing print files to it.  

If all else fails, perform the following action:  
·  Remove the memory stick from the printer.  
·  Restart your printer.  
·  Check the USB port free of foreign debris.  
·  Reformat the USB stick, place your print files on it, then safely remove it.  
·  Inserting the stick into the printer and verify files are displayed on the touch screen.  

If no resolve is presented, try a new USB stick.  

**How long do I have to shake the resin up or heat it?**

·  It is always best to read the resin's manufacturer's datasheet/instructions since every resin is particular and requires different mixing and operating temperature.

·  In most cases, resins don't like to be used below 21'C/70'F.

·  A non-pigmented resin getting a good shake for 30 seconds is enough, while a heavy pigmented one for a minute or two. If the resin is thicker due to low temp, add some extra time to that.

**How much resin should I pour into the vat?** 

To start, fill the VAT about halfway between the FEP surface and max fill line. Do not exceed the max fill line; if there is too much resin, it will rise from displacement and cause a spill. Once you pour resin into the VAT, let it sit for a few minutes to allow any air bubbles to escape before printing. 

**Can I add resin halfway through a print?**

·  Yes, no problem. You do not have to pause the print; just slowly and gently pour the resin into the vat. Make sure to not bump or touch the build-plate while pouring. Be mindful of displacement when adding resin. 

·  Make sure to mix the fresh resin well before adding. Try to ensure the resin temperature is the same.

**Can I pause halfway through a print?** 

Yes, you can pause at any time during your print. Resume as quickly as you can to ensure that your print will continue safely. However, it is generally not recommended as it will most likely leave a line at the layer where you paused. If you time your pause after a peel move, the chances of resuming without a line is better. 

**My print turned out OK but there resin 'skin' on the FEP?**

This is typical resin over-exposing during the printing process. Double-check your machine/resin exposure settings. It is very common to mistake resin exposure settings for the Mars vice Mars 2; this could differ from 10 seconds to 3 seconds.

**My print is stuck to the FEP! How should I remove it?**

· Unscrew the resin vat retaining screws and remove the vat.

· Empty the resin vat. The vat has one corner recessed to aid in pouring. Use the recessed corner in combination with a funnel and screen to pour the resin into the bottle. 

· Wipe the remaining resin into the funnel with a soft silicone squeegee and then with a soft paper cloth. The layer of hardened/stuck resin should now be discernible. 

· While the vat is in a normal upright position, grasp it with both hands, with fingers on the bottom side of the FEP and palms against the sides of it. Use your fingertips (not your fingernails) to detach the solidified resin from the FEP by gently applying pressing up. Start from the edges and use a circular motion to separate it evenly. You may be able to hear the layer detaching.

· You should now be able to remove the large pieces by using the plastic scraper to very gently slide across the FEP with the blade at a low shallow angle. 

· Once removed, proceed with normal after print cleanup, but pay particular attention to the FEP. Inspect the surface for any scratches, dents, or holes. If the FEP is damaged, replace it immediately.

**My prints are not dimensionally accurate!?!?**

First, ensure that your exposure settings are optimal for the resin used. Underexposure causes thinner parts, while overexposure will swell. Many of the basic resins swell when printed. There could also be slight shrinkage. It all depends on your settings and the brand of resin and formulations that manufacturers use. It usually isn't noticeable on organic prints. 

**How can I make them true to scale?**

Here is a process to determine a correction factor to use in your slicer.

- [ ] Log room temp.
- [ ] Do resin calibration prints, get it nailed. Write the temp and exposure seconds on the bottle.
- [ ] Make a cube or download one if lazy. 20mm cubes are typical, but the correction factor will be more accurate when you make it larger. If you typically print a standard sized object in the X & Y planes, then use a block outline of the shape you will print as the resin shrinkage may not be a true linear correction.
- [ ] Slice the .stl file as usual, at 100% scale.
- [ ] Print, wash and cure the object.
- [ ] Calculate the scaling factor:  
  Use the following formulas to determine the required scaling factor:  
  X Scaling Factor = (XCAD - XPART)/ XCAD * 100% (answer will be as a percentage)  
  EXAMPLE:  
  X measurement of CAD model = 20mm  
  X measurement of printed part = 18.5mm  
  X Scaling Factor = (20.0 – 18.5)/20.0 *100 = 7.5%  
  Slicer X scaling factor should be 100% + 7.5% = 107.5%      
- [ ] Go into your slicer, change X & Y scaling to the calculated correction factor and then slice the .stl file.
- [ ] Print, wash and cure the object.
- [ ] Measure the corrected print. If an error still exists, go back to the 'Calculate the scaling factor' step, but you will then subtract or add to the previously obtained scaling factor and then repeat the verification process.
- [ ] The last step, write the correction factor on the bottle.  

**Lines or Layer Shifting on the printed model?**

See Elegoo's support guide [here](https://www.elegoo.com/blogs/3d-printer-user-guide/lines-or-layer-shifting-on-the-printed-model).

**Holes in the 3D printed model?**

See Elegoo's support guide [here](https://www.elegoo.com/blogs/3d-printer-user-guide/holes-in-the-3d-printed-model).

**I hear a rumbling / loud humming noise once I start a print?** 

If you're having issues with the build-plate homing fine but then trying to bury itself into the LCD and making a rumbling/loud humming noise once a print is initiated - relevel the build-plate and ensure you use Z=0.

**I hear a strange faint knock or a suction/sticking sound every time the plate lifts. Is this normal?** 

It's completely normal. It's a good sign that your print is sticking to the build-plate and that the layers are releasing from the FEP film. It will be more audible during the first few bottom layers of the print, don't worry if you can't hear it later on as it depends on the layer section being printed. 

**How do I know that my print is sticking to the build-plate?** 

·  One easy way to tell is by listening for the sound that's made as the layer peels off the FEP. You can hear it clearly, especially for the first few bottom layers. Don't worry if you can't hear it anymore later; it varies depending on the layer's size being printed. 

·  You can also use the pause to check on your print, but note that you may get a line at the layer where you paused. 

**My prints just won't stick?** 

This is almost always a build-plate leveling issue. Make sure your leveling is 100% correct before attempting these other solutions. An easy way to check the level is by placing a sheet of paper between the LCD and build-plate - press the 'home' button and if done correctly, there should be some resistance when pulling the paper, just as when you leveled it. You can also try this at each corner of the build-plate. 

·  Preheat or warm the resin, you can use a hairdryer or heating pad on most bottles to gently heat the resin to 22~30°C. 

·  Shake your resin in the bottle well before using it. Resin already in the vat may have settled and need to be stirred. 

·  Clean the build-plate carefully with IPA or other solvents - dry before use. 

·  Preheat the build-plate, same as the resin. 

·  Did you remember to set, or reset, Z=0?  

·  Check your print and exposure settings.  

·  The FEP film may be too tight or too loose. 

·  You may be using bad resin, either very expired or contaminated with cleaning product, or a resin formulated for SLA laser or DLP printers. 

·  Are you using a specialty resin for casting such as Blue cast? You may need a primer coat. Check the resin manufacturer's recommendations. 

·  If all else fails, check your plate level once again and use Z=0! 

**The bottom layers stick, but my prints didn't form/fell off at the supports?**

See Elegoo's support guide [here](https://www.elegoo.com/blogs/3d-printer-user-guide/model-sticking-to-the-fep-rather-than-sticking-to-the-build-platform) and [here](https://www.elegoo.com/blogs/3d-printer-user-guide/print-falls-from-the-support-or-part-of-the-print-is-missing).

If your prints have good bottom adhesion but fail at the supports, this is generally due to your normal layers' incorrect exposure settings. As a first step, try increasing exposure. 

·  Try increasing normal exposures by a second or two. 

·  You may need to increase support tip size and depth in your slicer settings. 

·  A mix of medium and heavy supports will help and/or increase support density. 

·  It can also be due to the orientation of your model. Try to angle your model and minimize large surface sections. 

·  Is your model a large solid? Hollowing the model is recommended. 

**The top of my prints are sharp and detailed, but the bottoms seem soft and less defined?** 

During the printing process, the part remains in a semi-reacted or semi-cured state. While in this semi-reacted state, the resin retains polymerizable groups that can still form bonds across layers. Polymerization only stops when the resin is fully cured via post-processing in a UV station or sunlight. 

Simply put, during printing, the layers of the model facing the FEP film are always sharply defined as the layer is exposed perfectly against it. Whereas the layers facing the build-plate, previously exposed, still receive UV light from diffusion/diffraction/scattering from the current exposed layer and thus will still cure slightly. This is akin to overexposure and thus details will be lost. Coupled with this, some resin always remains around the bottom parts (facing the build-plate) and will also bond and cure to the details. 

This is a limitation of the technology but can be largely mitigated and overcome by the following:

·  Ensure that exposure settings are optimal for your resin. Overexposure will magnify this issue. 

·  Ensure that the model is well orientated and angled to minimize resin pooling and that important details are presented facing the FEP film. 

·  Allow enough clearance for the supports so that resin does not get trapped between the bottom of the print and the build-plate.

·  Set longer UV off-times so that more viscous resins can drain during lift. It will also help to heat the resin during colder temperatures. 

## :star2:CLEANING

**How do I clean my prints?** 

The recommended method is the two tub system. Fill both containers with 91% Isopropyl Alcohol (IPA) or other solvents such as 95% Ethanol. Although not necessary, heating the first tub to around 45°C helps dissolve the resin faster. 

Drop the print into the first tub and swirl for several seconds. Use a soft brush on hard to reach parts, crevices, etc. Then dunk the part in the second tub of solvent and rinse clean. Do not leave your prints soaking too long in the tubs - only enough time to remove the excess resin. 

Lastly, remove the part and dry thoroughly before UV curing; pat-drying with a lint-free cloth followed by blow-drying with compressed air or a hairdryer works well. Whichever way you choose - ensure the part is dried thoroughly before UV curing; failure to do so can result in loss of definition, white powdery remains on the part, and flaking/scaling on surfaces. 

**What solvents should I use to clean my prints?** 

Resin manufacturers universally recommend 91% Isopropyl Alcohol (IPA) or 95% Ethanol. Other solvents may be used but generally not recommended. Do not pay for overpriced cleaning solutions marketed for 3D resin printers. When in doubt, check the resin manufacturer's datasheet/recommendations. 

**How long do I clean my parts in solvents?** 

For as little time as possible to get your prints cleaned of uncured resin. Do not leave your prints to soak. Some manufacturers advise no longer than 30 seconds. Usually no more than 3 minutes. When in doubt, check the resin manufacturer's datasheet/recommendations. 

**How do I clean the LCD?**

Use a microfiber cloth and a small spray of IPA to remove any dust and stains. If there is dried resin on the glass, you can carefully scrape it off with a razor. Finally, buff the glass with a microfiber cloth.

**The FEP tore, and there's cured resin on the LCD. How do I clean that?** 

Damp a piece of a microfiber cloth with IPA, then lay it on the cured resin. Wait a few minutes, then with a fingernail, gently try to prise the layer of cured resin off the LCD glass. If you can't easily prise it off, use a razor or glass scraper, but be careful with that. Be prepared to purchase a replacement LCD.

**How do I clean the FEP Film?**

Once you have drained the vat of resin, spray down with IPA and gently wipe it off with a microfiber cloth. Spray again and use the microfiber cloth to soak off the remaining residue from the FEP. You may need to repeat this several times. Finally, buff the FEP with the microfiber cloth. Be careful of dried resin on the cloth that could scratch or puncture the FEP. 

**What else can I use to clean my prints and tools from uncured resin?**

·  Manufacturers universally advise using a solvent like 91% IPA (Isopropyl Alcohol) or 95% Ethanol. Proprietary cleaning solutions or other solvents may also be used, such as Mineral spirits (aka White spirits, Turpentine), etc. 

·  If you have bought a water-washable resin, you can simply use water and some mild soap. 

·  A small brush helps get into and clean the fine grooves or details in your prints.

·  Alcohol and other flammable solvents should not be used directly with ultrasonic cleaners because of the fire hazard.

**How long can I keep the resin in the vat?**

It depends on environmental factors and type/brand of resin. Typically if the resin is kept out of light and spared any moisture/dirt, it may sit in the vat for a few weeks. Clear resins tend to sit better; opaque resins will need more stirring before use to mix the pigments back. When in doubt, check the resin manufacturer's datasheet/recommendations. 

·  Check for loose cured resin or stuck resin; you will need to clean that out. 

·  Cover the vat. You can cut a piece of cardboard that fits over the vat or print one out on an FDM printer.

·  Before printing, carefully stir the resin for 1 - 2 minutes with a soft silicone spatula, be careful not to scratch the FEP screen.

·  Do not leave the build-plate hanging with uncured resin. Take it out and clean with IPA - leave it out until you are ready to print. This will lessen the weight on the single lead screw prevent deformation and potential Z wobble. 

**Can I put excess resin that didn't get used during a print back into the original bottle?**

Yes, but always strain out any debris using a filter! The resin vat has one corner recessed to aid in pouring. Use the recessed corner in combination with a funnel (screen placed inside the funnel) to pour the resin back into the bottle. Inspect the FEP's surface for any scratches, dents, or holes. If the FEP is damaged, replace it immediately.

**Water washable resin, how to dispose of the dirty water after washing the print? Wash it down the drain?** 

**Do not pour it down the drain!** Water washable resin works because it uses water-soluble monomers. Water isn't an acrylate. Water can not cure. When you dilute resin into anything that's not capable of curing, it won't be inert again. 
The only proper way to dispose of the wash is to reduce the solution by evaporation, and then collect and UV cure the resin residuals and dispose of them properly. 

## :hammer:POST PROCESSING

**My print stuck so well to the build-plate that I can't remove it?** 

When prints adhere so well that removal is difficult, use the provided sharpened steel scraper to fracture the model off the plate. Place the build-plate/print on your working surface, in a position where the model is facing left and adjustable head facing right or vice-versa. While using a very low, near-parallel to the build-plate angle, position the steel scraper on the edge where the model and build-plate interface and then give a quick, gentle downwards knock to the handle. Running hot water over the print/build-plate for several seconds may provide additional assistance.

**When should I remove supports?** 

It is generally best to first clean the entire print before removing any supports - this will reduce your and the work area's resin exposure. Following the cleaning process, remove the supports before UV curing as they are softer, and in many cases, you can easily pull or rub them off. In some cases, you may want to remove them after curing, especially when working with thin and delicate parts that may warp during the curing process if not supported.

**What is post-curing?**

Post-curing enables your printed parts to reach the highest possible strength and become more stable. Many post-curing methods exist using light and heat, from curing only with natural sunlight, using salon type UV fingernail curing stations, to DIY UV curing stations. Heat accelerates the process and enables even more complete bond formation, resulting in increased material properties impossible to achieve with light alone. For small prints, a low-cost UV nail salon might be an effective post-curing tool. But to maximize mechanical properties, consider purchasing an enclosure around a powerful 405 nm light.

**How long should I cure my print?**

The proper light, heat, and time will optimize your prints' mechanical properties. Post-cure time depends on your equipment, resin choice, and part geometry. An ideal post-cure setting achieves the properties you need in the shortest amount of time. For standard resins, this amount may be as short as 10 minutes, going up 30 minutes. Where strength, rigidity, and temperature resistance are needed, engineering grade resins improve with post-cure up to 60 minutes. Always check the resin manufacturer's datasheet/recommendations as each different brand and kind of resin will differ. 

**What will happen with over-curing?**

The material will degrade due to UV irradiation. With extreme UV exposure levels, the part will degrade and cause brittleness. Placing a part outside is generally not nearly enough to cause any notable amount of degradation. But curing a part overnight in a high-intensity UV chamber might be enough to damage the material. This is not unique to resin and would occur in most organic materials.

**Will curing prints underwater speed up the curing time?**

Yes. Underwater heat dissipation and UV diffuse scattering effect will be better. The water does absorb UV light, but the absorption is not significant at the wavelengths used to cure UV resin. So you don't have to add much exposure time if you cure your parts in a shallow tank of water. There are really no "cons" to curing in a water bath, other than getting your parts wet and require drying.

**Is post-curing with sunlight useful?** 

If you don't have a UV chamber, you can submerge the print in a clear container filled with water, as said above. Then place the container under direct sunlight. Of course, the exposure time will be much longer than under a direct UV lamp. If the print still feels uncured or sticky, leave the print and the container in the sun for some more time.

**How durable are the prints? Will they break if I drop them?** 

It depends on the resin used. Unlike PLA or ABS, regular hobby-grade resin prints are quite brittle and can easily break when dropped. There are specially formulated resins for prototyping or even functional usage, which have different properties such as flexibility, hardness, and UV resistance. 

**Why do I get white chalky residue on my prints after curing?** 

The white residue appears if there's moisture, water, or uncured resin on your prints when UV cured. Always clean your prints well and make sure they are completely dry before the UV curing. 

## :ocean:FEP MAINTENANCE

When you receive your new printer, it will come with an aluminum or plastic vat frame with FEP film already installed. Check that the film is tight by lightly tapping with your finger. If it is tensioned correctly, it should sound just like a snare drum. 

Sometimes the screws may seem loose, but they may be tensioned correctly from the factory. Do not merely tighten the screws, as you may over tension the FEP. 

**How tight exactly should the FEP be tensioned?** 

If it sounds like a snare drum when you lightly tap with a finger, it should be good enough. But since hearing is subjective, to be precise, you should use an audio analyzer to check; factory tensioned FEP film is around 350Hz, but anything between 250Hz to 375Hz is fine. [This](https://youtu.be/Yr_wtZqBfbQ) video shows how to tune/tension your FEP.

**Why do I have to go through all this trouble to get the correct FEP tension?** 

When your print peels from the FEP film, there are a lot of suction forces involved. Unlike more expensive machines, it does not have a tilt peel mechanism; therefore, it relies on the FEP film's flexibility to provide a clean and successful peel. 

*If the film is too tightly tensioned, your prints won't peel off properly and may stick to the build-plate, too loosely tensioned, and it'll have layer lines or other unwanted artifacts.*

A correctly tensioned FEP at a normal room temperature will give the best print results and avoid print failures or delamination problems. 

**Should I coat my FEP film?**

Not needed in most cases, FEP (fluorinated ethylene propylene, invented by DuPont, sold under the brand name Teflon FEP) is already one of the most slippery materials known to science. With that being said, many users report increased success rates with different coatings but caution must be taken as applications and compounds vary from case to case.

**Why is my FEP film so cloudy or hazy?** 

When new, the film is clear. But it is easily scratched by handling or cleaning. Use a soft tissue to soak resin when cleaning up the vat, do not aggressively wipe the film as even tissue will scratch it. These micro scratches cause the film to go cloudy. Buffing the film with a microfiber cloth will restore some clarity. The film must be kept clear to ensure sharp and detailed prints. 

**When should I replace my FEP film?** 

If you take care of it, it will not need to be replaced for months. You should only need to replace the FEP film when it becomes scratched up or cloudy. If it is not correctly maintained, your print quality will deteriorate. Replace it immediately if it is punctured or torn. If you notice cured resin on your LCD glass, it means the film may have a micro tear.

**How do I replace the FEP film?** 

Watch the video by Elegoo detailed step by step [here](https://youtu.be/tsokPTRLXss). It is important to note one significant neglect in that video: there is no mention of tightness! Watch the below video for that. It is also much easier to trim the excess FEP before placing the retaining assembly into the VAT frame. 
FEP replacement video using Gatorade bottle cap [here](https://youtu.be/Yr_wtZqBfbQ). 

**How do I test if my FEP film has protective plastic on it?** 

It's difficult to see if there's a protective plastic film on your FEP. An easy way to test is by dripping a few drops of resin on your FEP film, then hold the film vertically. If the resin slides downward easily without sticking and leaves the FEP clear, it's good. If the resin sticks where you dripped it and moves slowly or smears, you have protective plastic that needs to be removed. 

**Why do I need to use a bottle cap or foam when replacing the FEP film?** 

The bottle cap, or foam, will allow some slack to the film so that when you tighten the frame down, you will get approximate tension. If you don't do that, you may over tension the film and it may tear. If it didn't tear, later on you'll be wondering why all your prints fail. 

## :nut_and_bolt:PRINTER MAINTENANCE

**What maintenance do I need to do to keep my printer running well?** 

·  Keep your printer clean! Keep everything clean by wiping down with a microfiber cloth slightly dampened with IPA. Wipe resin drops and spills off immediately with IPA and tissue.

·  Keep your vat and FEP clean. Empty the resin vat after each print failure. The vat has one corner recessed to aid in pouring. Use the recessed corner in combination with a funnel and screen to pour the resin into the bottle. Inspect the FEP's surface for any scratches, dents, or holes. If the FEP is damaged, replace it immediately.

·  Keep the LCD screen clean. Use a microfiber cloth dampened with IPA or LCD cleaning spray to clean to surface. Do not use paper towels; otherwise, you may scratch the LCD surface. 

·  Dust off and keep the printer's cover clean. Clean the lid with IPA, but do not use ethanol or acetone. 

·  Clean and Grease Z-Screw. Depending on usage frequency, every two months or earlier, clean and replace the grease on the lead screw. If it squeaks, do this immediately. 

Peter Grande has a good video on general maintenance; you can find it [here](https://youtu.be/2178v1iMSqo). 

**What grease should I use for the lead screw (Z rod)?**

Use a PTFE based such as Super Lube or white lithium viscous grease. It should be a thick, creamy, toothpaste consistency type. You can use a generic machine grease, cosmoline, gel grease, gear grease, or similar but make sure the lubricant is not thin and runny, and Do NOT use WD-40!
Watch the Official Elegoo instructional video [here](https://youtu.be/OWXlZSi15cE).

**How do I replace the grease on the lead screw?** 

Wipe all the old dirty grey grease off with a cloth rag or kitchen towels. Then really get it clean by wiping again with solvent and use a toothbrush to get between the threads. IPA works great. Make sure solvent doesn't drip down into the stepper motor beneath. When it's clean and dry, re-grease with good quality grease, apply by dabbing onto the entire length of the screw, then switch on the printer and run the slide block up and down. 

**How do I replace the LCD screen?**

Watch the Official Elegoo instructional video [here](https://youtu.be/JYxKFs2lY8w).

**How do I replace the Z limit switch?**

Watch the Official Elegoo instructional video [here](https://www.youtube.com/watch?v=tBmwPHZfxI8).

**How do I replace the front touch screen?**

Watch the Official Elegoo instructional video [here](https://youtu.be/45wycTFA9E0).

**Where can I buy replacement parts?**

From Elegoo's website [here](https://www.elegoo.com/collections/parts-accessories), or Chitu Systems [here](https://chitusystems.com/).

**Where can I find firmware updates, original manual, original USB drive files, and resin settings?**

From Elegoo's website [here](https://www.elegoo.com/pages/3d-printing-user-support).

## :heavy_check_mark:CONSUMABLE ITEMS

There are many consumables available for resin printing, and this is just a brief list to give you some ideas. In addition to this consumables list, you will need resin. There are several kinds of resins; standard, high-definition, flexible, castable, high-temperature, and more. Each resin presents its unique strengths and weaknesses, but the standard type is usually best to start while getting comfortable with the resin printing process. With that, when selecting a resin, make sure that it is compatible with your machine - which is an MSLA LED/LCD unit with a 405nm light source. Please pay attention to the resin manufacturer's recommended operating temperature to ensure that it will be usable in your environment.   

**Tier 1 - Critical Items. These are the typical use items that you should have on hand.**  
*Metal Scraper  
*Plastic Scraper  
Plastic Razor Blades  
Nitrile Gloves  
Safety Glasses  
Mask / Respirator   
Paint Filters  
Small Funnel for Paint Filters  
Small Soft Silicone Squeegee  
Paper Towels  
Microfiber Cloth Pack  
Isopropyl Alcohol  
Small Paint Brush (or toothbrush)  
Windex Foaming Spray  

**Tier 2 - Recommended Items. Items that you will eventually need or will make the machine's operation safer & more manageable.**  
Replacement FEP Film  
Craft Apron  
Quality USB Stick  
Silicone or Boot Mud Mat  
or Cafe Serving Tray  
Super Lube PTFE Grease  
Exacto Knives  
Pickles Bucket w/ Basket  

**Tier 3 - Helpful Items. These are items that you don't need per se, but they will be helpful.**  
Clean & Wash Station  
or Ultrasonic Cleaner  
Replacement LCD Screen  
Printer Enclosure  
Small/Micro file set  
UV Flashlight  
Hex Driver Set  
^Resin VAT Cover  
^Top Cover Handle  
^Dual Angled Drip Attachment  

*Included with the printer.  
^Can be printed or purchased.  

## :thumbsup:ACKNOWLEDGMENTS

**Where did all this information come from?** 

Information was gathered from the [Photonsters](http://photonsters.org), [Elegoo product site](https://www.elegoo.com/), [Chitubox](https://www.chitubox.com/en/support/indepth/technology), [ElegooMars Reddit Sub](https://www.reddit.com/r/ElegooMars/), and various others.  
Photonsters.org is a wealth of information, always worth is visit, even if you don't have a Photon... 

:zap: If you have any suggestions for a change, addition, or correction to this guide - please feel free to either submit it via form [here](https://github.com/rkolbi/My_Mars2Pro_Accessories/issues/new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) or in the discussions page [here](https://github.com/rkolbi/My_Mars2Pro_Accessories/discussions/categories/printer-guide).

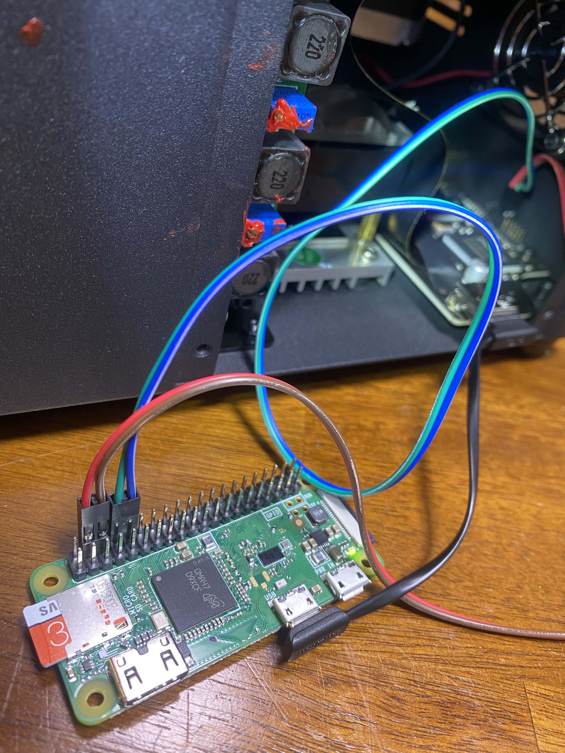
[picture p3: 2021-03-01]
Tools_&_Information/my-mariner-configs/mariner-rpi-saturn.jpeg

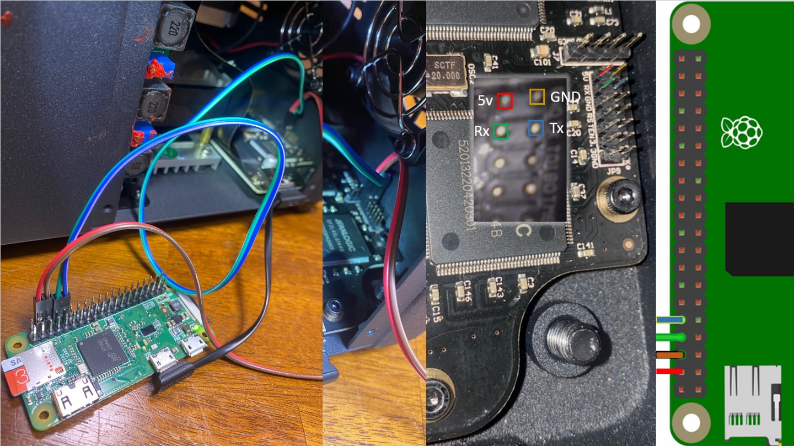
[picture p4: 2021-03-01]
Tools_&_Information/my-mariner-configs/mariner-saturn-rpi.jpg

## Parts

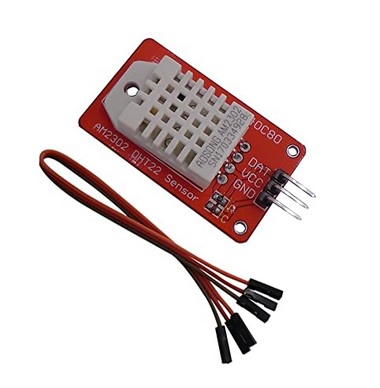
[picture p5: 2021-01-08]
Parts_STLs/MARS2-DHT22-Assm.jpg

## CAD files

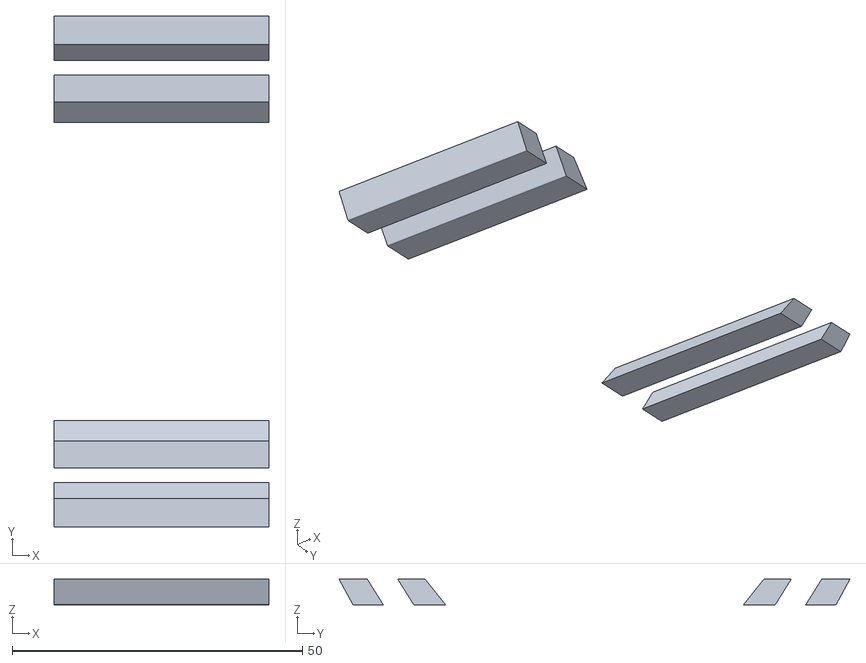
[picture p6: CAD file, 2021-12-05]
Parts_STLs/LED_Shade_Part2-Pegs(1_needed).STL
37.0 x 88.0 x 4.40

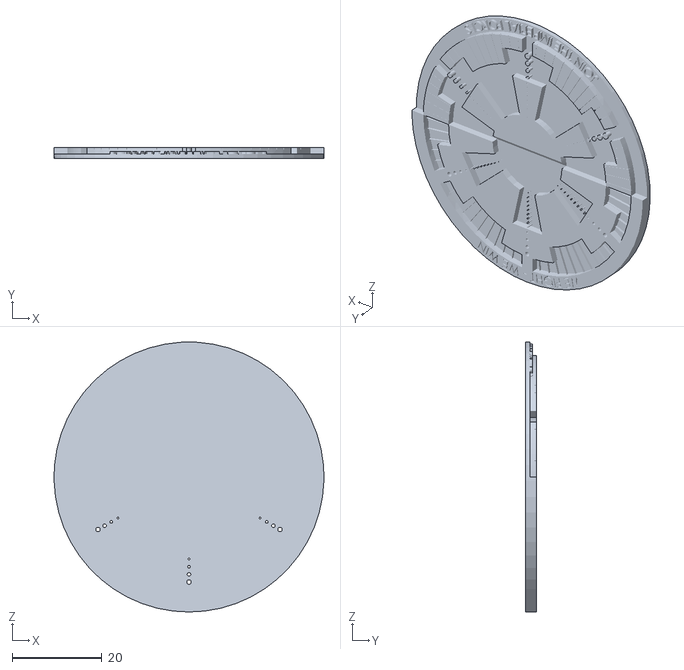
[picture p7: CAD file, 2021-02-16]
Resin_exposure_testing/STLs/Imperial test/RECRUITMENT-COIN_V2-RAW.STL
60.0 x 2.50 x 60.0

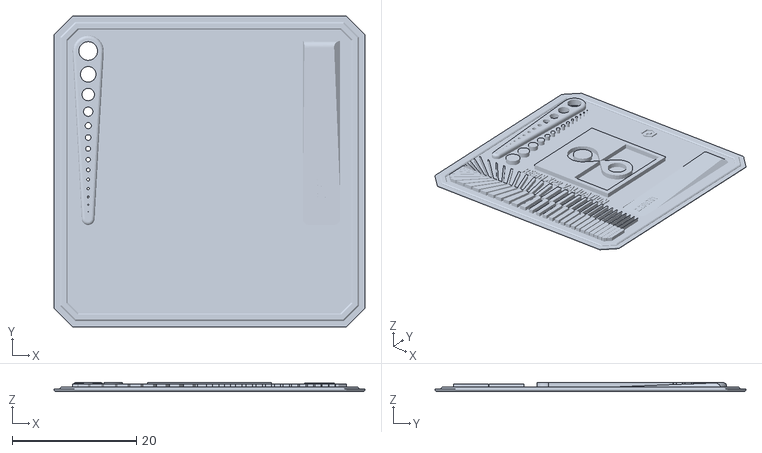
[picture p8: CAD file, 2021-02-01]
Resin_exposure_testing/STLs/ResinXP2-Calibration.stl
50.0 x 50.0 x 1.40

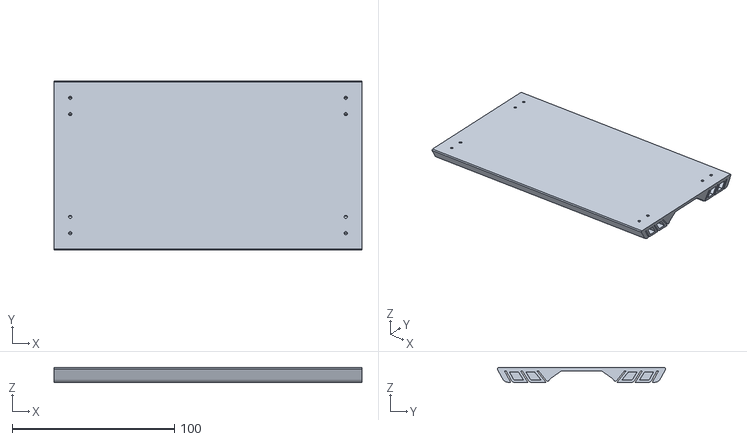
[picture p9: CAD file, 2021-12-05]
Parts_STLs/LED_Shade_Part3-Base(2_needed).STL
190.0 x 104.0 x 9.00

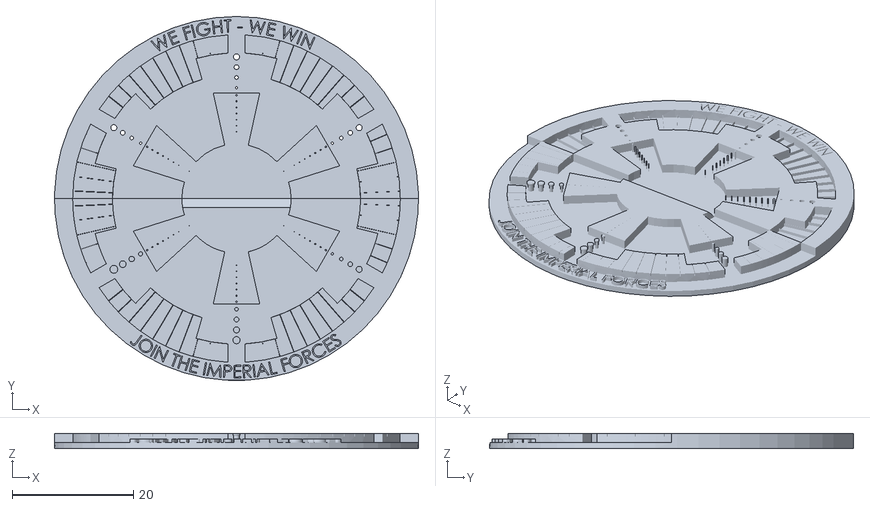
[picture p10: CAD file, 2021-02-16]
Resin_exposure_testing/STLs/Imperial test/RECRUITMENT-COIN_V2-Repaired.STL
60.0 x 60.0 x 2.50

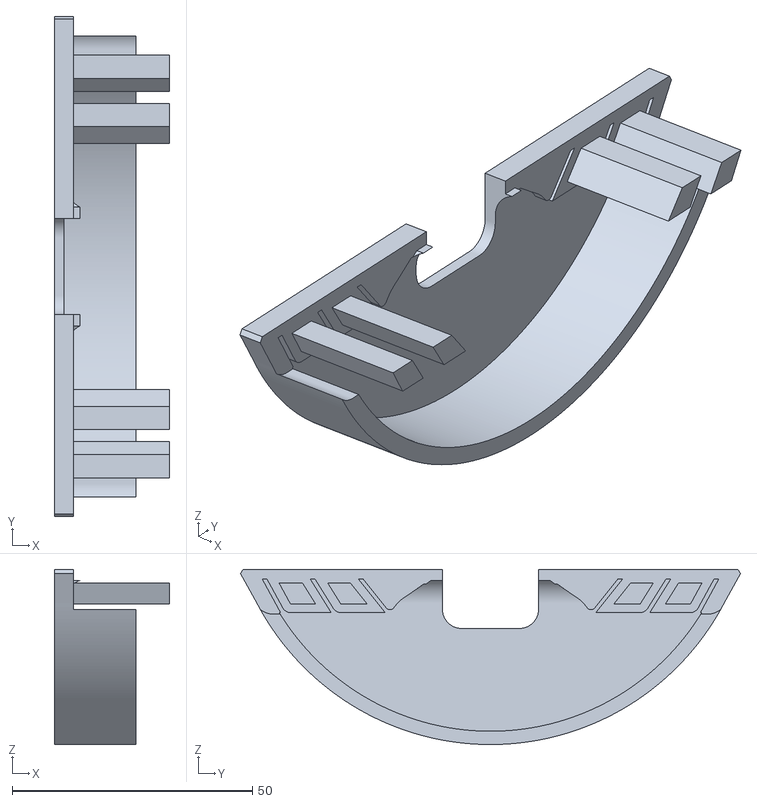
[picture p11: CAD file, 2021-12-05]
Parts_STLs/LED_Shade_Part1-EndCap(2_needed).STL
24.0 x 104.0 x 36.4

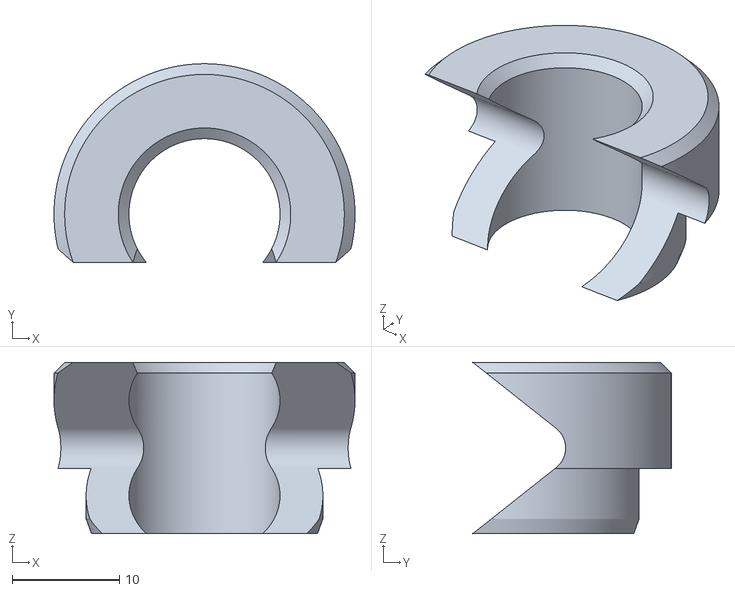
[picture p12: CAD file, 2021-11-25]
Parts_STLs/motor-saver-split-A.STL
28.1 x 18.5 x 16.0

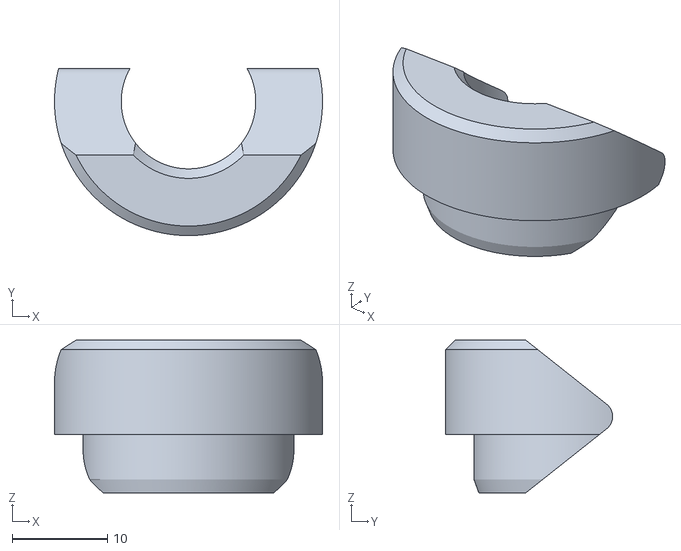
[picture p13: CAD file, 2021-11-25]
Parts_STLs/motor-saver-split-B.STL
28.1 x 17.5 x 16.0

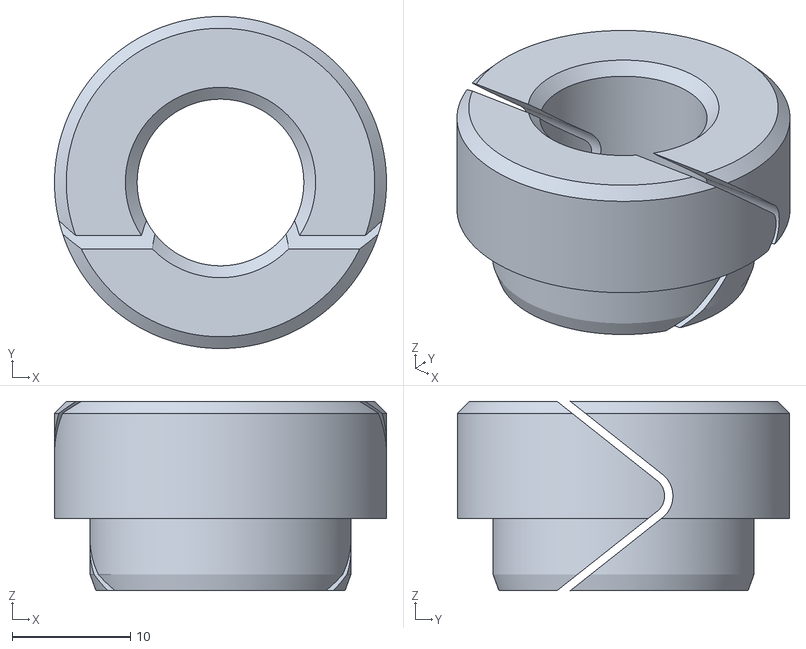
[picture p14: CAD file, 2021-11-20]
Parts_STLs/motor-saver-split.STL
28.1 x 28.1 x 16.0

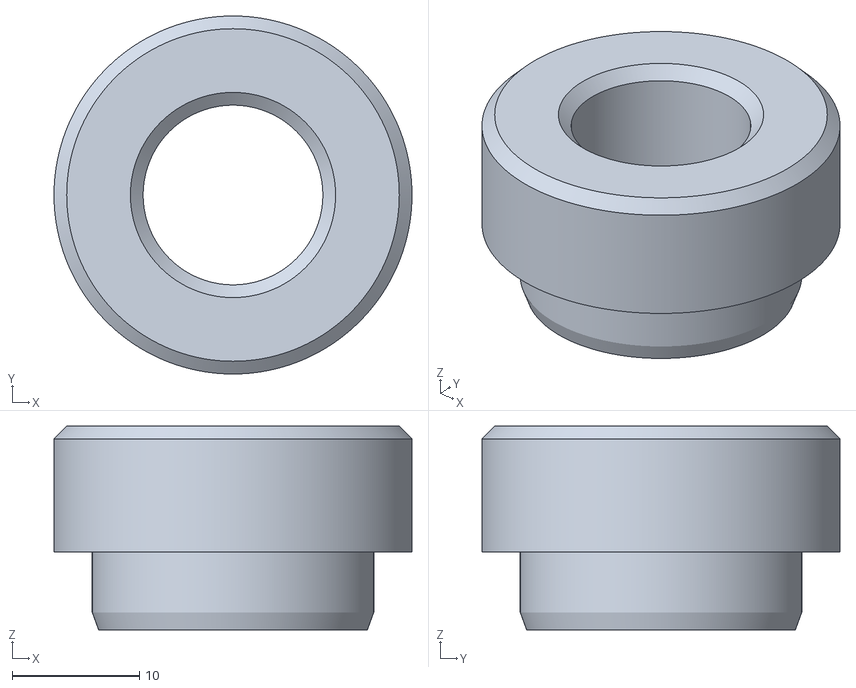
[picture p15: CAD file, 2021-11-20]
Parts_STLs/motor-saver.STL
28.1 x 28.1 x 16.0

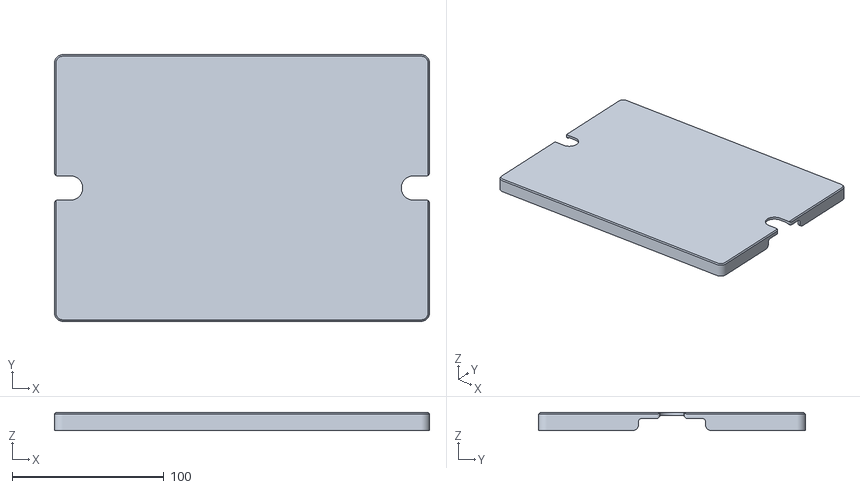
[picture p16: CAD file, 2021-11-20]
Parts_STLs/Saturn-Vat-Cover.STL
247.5 x 176.0 x 12.0

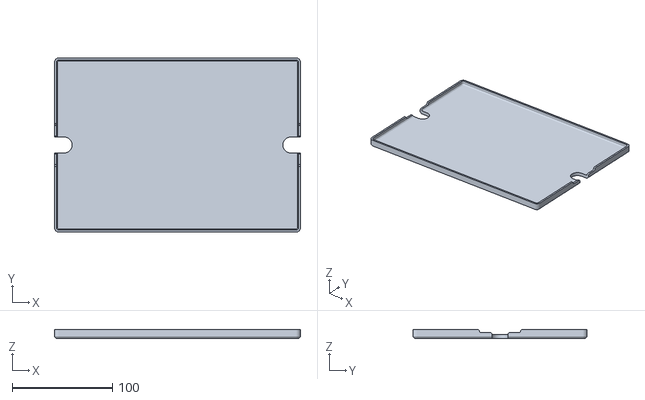
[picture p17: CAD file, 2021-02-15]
Parts_STLs/SATURN_Vat_Top_BETA.STL
245.5 x 174.0 x 9.00

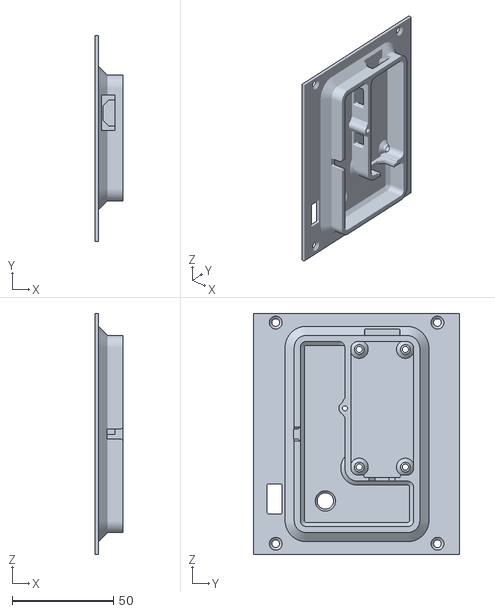
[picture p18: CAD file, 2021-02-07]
Parts_STLs/SATURN-rpiW-Case_Sideplate-b.STL
13.9 x 101.7 x 119.0

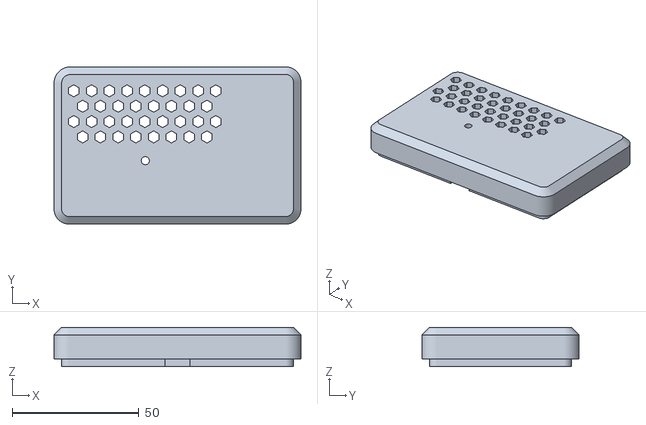
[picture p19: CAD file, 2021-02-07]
Parts_STLs/SATURN-rpiW_Case_Cover.STL
97.4 x 62.0 x 15.5

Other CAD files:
Parts_STLs/SATURN-rpiW-Case_Sideplate-a.STL
Parts_STLs/MARS2-rPiW_Small-DHT22 - Case.STL
Parts_STLs/MARS2-DHT22-Z_Tower-b.STL
Parts_STLs/MARS2Pro-Vat-Top(installed).STL
Parts_STLs/MARS2-rPiW_Case_Bottom.STL
Parts_STLs/MARS2-rPiW_Case_Top.STL
Parts_STLs/MARS2Pro-Vat-Bottom(not-installed).STL

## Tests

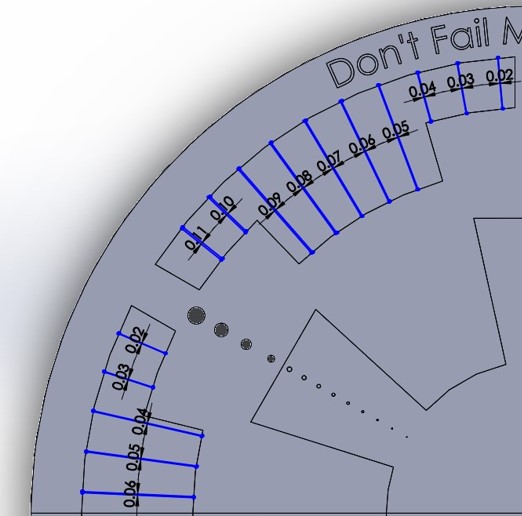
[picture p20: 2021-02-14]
Resin_exposure_testing/STLs/Imperial test/Imperial-resin-v4-e.jpg

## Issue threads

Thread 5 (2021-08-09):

Mounting holes in the SATURN-rpiW-Case_Slideplate do not match with the SATURN case.

TMillesich, 2021-08-09:
Affected files:
SATURN-rpiW-Case_Sideplate-a.STL
SATURN-rpiW-Case_Sideplate-b.STL

The mounting holes in the plate do not match with the Saturn case. Only by few millimeters, but enough to miss both tapped holes on a short edge and another one needs some filing for the tapped hole.

I'll check that i can get the correct positions with my sliding caliper and fusion360 a new STL.

rkolbi, 2021-11-21:
This is the only report of the fitment not being correct. Please let me know what version of the Saturn you are using, what and how you printed this file, and what were you're exact findings with fitment.

Closed 2021-11-21.

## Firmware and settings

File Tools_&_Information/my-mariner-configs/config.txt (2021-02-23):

# For more options and information see
# http://rpf.io/configtxt
# Some settings may impact device functionality. See link above for details

# uncomment if you get no picture on HDMI for a default "safe" mode
#hdmi_safe=1

# uncomment this if your display has a black border of unused pixels visible
# and your display can output without overscan
#disable_overscan=1

# uncomment the following to adjust overscan. Use positive numbers if console
# goes off screen, and negative if there is too much border
#overscan_left=16
#overscan_right=16
#overscan_top=16
#overscan_bottom=16

# uncomment to force a console size. By default it will be display's size minus
# overscan.
#framebuffer_width=1280
#framebuffer_height=720

# uncomment if hdmi display is not detected and composite is being output
#hdmi_force_hotplug=1

# uncomment to force a specific HDMI mode (this will force VGA)
#hdmi_group=1
#hdmi_mode=1

# uncomment to force a HDMI mode rather than DVI. This can make audio work in
# DMT (computer monitor) modes
#hdmi_drive=2

# uncomment to increase signal to HDMI, if you have interference, blanking, or
# no display
#config_hdmi_boost=4

# uncomment for composite PAL
#sdtv_mode=2

#uncomment to overclock the arm. 700 MHz is the default.
#arm_freq=800

# Uncomment some or all of these to enable the optional hardware interfaces
#dtparam=i2c_arm=on
#dtparam=i2s=on
#dtparam=spi=on

# Uncomment this to enable infrared communication.
#dtoverlay=gpio-ir,gpio_pin=17
#dtoverlay=gpio-ir-tx,gpio_pin=18

# Additional overlays and parameters are documented /boot/overlays/README

# Enable audio (loads snd_bcm2835)
dtparam=audio=on

[pi4]
# Enable DRM VC4 V3D driver on top of the dispmanx display stack
dtoverlay=vc4-fkms-v3d
max_framebuffers=2

[all]
#dtoverlay=vc4-fkms-v3d
dtparam=act_led_trigger=actpwr
dtoverlay=dwc2,dr_mode=peripheral
enable_uart=1

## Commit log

2021-01-13 Create Getting a print started.md
2021-01-15 Delete Layer-thickness vs exposure.xlsx
    moves into tools folder
    [Layer-thickness vs exposure.xlsx]
2021-01-15 Delete delaytime.xlsx
    Moved into tools folder
    [delaytime.xlsx]
2021-01-15 Delete Getting a print started.md
    Moved to tools & information folder
2021-01-17 Update Getting a print started.md
2021-02-14 Is the force strong with your exposure?
    [IL2.STL]
2021-02-15 Organizing files
    [DHT22-Mars-Z_Tower-b.STL, IL2.STL, MARS2-DHT22-Z_Tower-b.STL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]
2021-02-16 Update from Desktop
    [RECRUITMENT-COIN_V2-RAW.STL, RECRUITMENT-COIN_V2-Repaired.STL]
2021-11-20 Add files via upload
    Vat cover has been slightly enlarged, Beta version is a very tight fit. Motor saver has two files, one split, one solid. Use split version if you do not want to take apart z drive to place it. In either case, use a bit of silicone adhesive between mating surfaces.
    [Saturn-Vat-Cover.STL, motor-saver-split.STL, motor-saver.STL]
2021-11-23 Add files via upload
    Exposure calibration print file, testing 1.8 seconds to 2.7 seconds in .15 seconds steps. See https://github.com/sn4k3/UVtools
2021-12-07 Add files via upload
    Minor calculation error corrected.
    [delaytime.xlsx]
